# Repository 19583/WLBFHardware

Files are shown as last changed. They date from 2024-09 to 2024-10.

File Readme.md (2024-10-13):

<!--
 * @Date: 2024-09-03 09:58:07
 * @LastEditors: Towers
 * @LastEditTime: 2024-10-13 19:57:09
-->

# WLBF Hardware

合肥工业大学宣城校区摩托组宛陵毕方硬件部分开源  
更新应该告一段落了  

### 文件目录说明

```
WLBFHardware 
├── 01_DRV8701Driver        #双电机驱动
│  ├── 01_DRV8701Driver.pdf #工程原理图
│  ├── ASM                  #组装/贴片坐标
│  ├── BOM                  #物料表    
│  ├── CAM                  #Gerber文件
│  ├── PRJ                  #项目文件
├── 02_PowerPart            #电源部分
├── 03_SigPart              #信号部分
├── 04_InterfacePart        #编码器、摄像头一体转接板
├── 05_LightDriver          #灯板驱动
├── 06_B&RLight             #红蓝双色灯板
├── LICENSE                 #开源许可
├── Readme.md

```

### 作者

Towers  

qq:1946459294    

 *您也可以在贡献者名单中参看所有参与该项目的开发者。*

### 版权说明

该项目签署了GUN 授权许可，详情请参阅 [LICENSE.txt](https://github.com/19583/WLBFHardware/blob/main/LICENSE)

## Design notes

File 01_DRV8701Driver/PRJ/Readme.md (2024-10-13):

<!--
 * @Date: 2024-10-13 19:29:54
 * @LastEditors: Towers
 * @LastEditTime: 2024-10-13 19:35:22
-->
# DRV8701Driver  
该板是用AD22画的，有元件库依赖的问题，还不知道怎么解决，未来研究明白了可以考虑开源  
这只是个DRV8701双驱，也没有做电流采样，而且设计上我觉得有些小问题，相关的开源很多，大家可以多看看，打板完如果不能正常工作，第一个应该检查焊接，第二个可以重点关注nFault引脚电平以及DataSheet上的相关描述（TI的手册还是写的很好的）

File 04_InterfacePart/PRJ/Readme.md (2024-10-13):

<!--
 * @Date: 2024-10-13 19:13:34
 * @LastEditors: Towers
 * @LastEditTime: 2024-10-13 19:23:15
-->
# 04_InterfacePart  
该板同时集成了编码器转接板和摄像头转接板  
但是输入端MX1.25的线序是反的，后续是靠反焊接口解决的  
有想改回来，但是一方面时间安排紧张，另方面我们也因为各种原因放弃了速度闭环，就没有继续改，所以现在我这里也是个半拉工程  
因此这部分就不放工程文件和贴片坐标文件，只放改之前的原理图、打板文件和BOM表了

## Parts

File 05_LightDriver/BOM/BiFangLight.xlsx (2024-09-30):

Comment | Description | Designator | Footprint | LibRef | Quantity
4.7uF 25V X5R | 贴片瓷片电容; MLCC; 0603(1608); | C1 | 0805C | 4.7uF 0603 25V X5R | 1
100nF 50V X7R | 贴片瓷片电容; MLCC; 0603(1608); | C2, C5, C6 | 0805C | 100nF 0603 50V X7R | 3
470nF 50V X7R | 贴片瓷片电容; MLCC; 0603(1608); | C3, C4 | 0805C | 470nF 0603 50V X7R | 2
LED_Dot_Matrix 7x15 | 逐飞科技 7x15 LED点阵 | D1 | LED_DOT_MATRIX 7X15 | LED_Dot_Matrix 7x15 | 1
Header-D-M 2x11P | 2x11pin, 直插, 双排针 | P1 | HDR2X11-M | Header-D-M 2x11P | 1
AO3401 | P-Channel SOT-23 MOSFET | Q1, Q2, Q3, Q4, Q9, Q10, Q11 | SOT-23 | AO3401 | 7
S8050 | NPN 三极管 | Q5, Q6, Q7, Q8, Q12, Q13, Q14 | SOT-23 | NPN S8050 | 7
3.3K ±1% | 贴片电阻 | R1, R2 | 0805_Res | Res-Chip_1 | 2
4.7K ±1% | 贴片电阻 | R3 | 0805_Res | Res-Chip | 1
1K ±1% | 贴片电阻 | R4, R5, R7, R9, R11, R13, R15, R17 | 0805_Res | Res-Chip_3 | 8
10K ±1% | 贴片电阻 | R6, R8, R10, R12, R14, R16, R18, R24 | 0805_Res | Res-Chip_2 | 8
100R ±1% | 贴片电阻 | R19 | 0805_Res | Res-Chip_4 | 1
100K ±1% | 贴片电阻 | R20, R21, R22, R23 | 0805_Res | Res-Chip_5 | 4
TLD7002-16ES | TLD7002-16ES LED驱动芯片 | U1 | TSDSO-24 | TLD7002-16ES | 1
LMV321 | LMV321 单通道轨对轨运放 | U2 | SOT-23-5 | LMV321 | 1
ZX-PZ2.54-1-15PZZ | 插针结构:1x15P;间距:2.54mm;行距:-;圆针/方针:方针;安装类型:直插;排数:单排;总PIN位数:15P;额定电流:3A;额定电压:1kV;配合针长度:6mm;塑高:2.5mm;端接针长度:3mm;触头材质:黄铜;触头镀层:金;工作温度范围:-40℃~+105℃;焊接温度(最大值):-;颜色:黑色; | U3 | HDR-TH_15P-P2.54-V-M | ZX-PZ2.54-1-15PZZ | 1

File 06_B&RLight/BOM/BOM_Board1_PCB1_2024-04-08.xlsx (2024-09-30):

No. | Quantity | Designator | Comment | Footprint | Value
1 | 1 | H1 | PZ254-1-14-Z-8.5 | HDR-TH_14P-P2.54-V-M
2 | 105 | LED1,LED2,LED3,LED4,LED5,LED6,LED7,LED8,LED9,LED10,LED11,LED12,LED13,LED14,LED15,LED16,LED17,LED18,LED19,LED20,LED21,LED22,LED23,LED24,LED25,LED26,LED27,LED28,LED29,LED30,LED31,LED32,LED33,LED34,LED35,LED36,LED37,LED38,LED39,LED40,LED41,LED42,LED43,LED44,LED45,LED46,LED47,LED48,LED49,LED50,LED51,LED52,LED53,LED54,LED55,LED56,LED57,LED58,LED59,LED60,LED61,LED62,LED63,LED64,LED65,LED66,LED67,LED68,LED69,LED70,LED71,LED72,LED73,LED74,LED75,LED76,LED77,LED78,LED79,LED80,LED81,LED82,LED83,LED84,LED85,LED86,LED87,LED88,LED89,LED90,LED91,LED92,LED93,LED94,LED95,LED96,LED97,LED98,LED99,LED100,LED101,LED102,LED103,LED104,LED105 | XL-3528SURUGC | LED-SMD_4P-L3.2-W2.8-LS3.5-TL
3 | 1 | U1 | ZX-PZ2.54-1-15PZZ | HDR-TH_15P-P2.54-V-M

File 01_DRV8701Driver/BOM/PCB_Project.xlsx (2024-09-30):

Comment | Description | Designator | Footprint | LibRef | Quantity
HX SS12D10G4 |  | 1 | SW-TH_SHOU-HAN_SS12D10G4 | HX SS12D10G4 | 1 | 5
RVT220UF16V67RV0015 | 容值:220uF;精度:±20%;额定电压:16V;纹波电流:110mA@120Hz;等效串联电阻:-; | C1 | CAP-SMD_BD6.3-L6.6-W6.6-FD | RVT220UF16V67RV0015 | 1 | 5
1uF |  | C3, C4, C8, C12, C13, C15 | 0805C | C1608X7R1C105K | 6 | 30
100nF |  | C7, C9, C10, C11, C14, C16 | 0805C | C1608X7R1H104K | 6 | 30
1N5819WS S4_C2927280 |  | D1, D2 | SOD-323_L1.6-W1.3-LS2.7-RD | 1N5819WS S4_C2927280 | 2 | 10
红色 |  | DV1, DV2 | 0805D | LTST-C171GKT | 2 | 10
TPH1R403NL/CSD18532Q5B |  | Q1, Q2, Q3, Q4, Q5, Q6, Q7, Q8 | LQ_SON5X6 | CSD18532Q5B | 8 | 40
10K |  | R1, R4, R5, R6, R7, R8, R9, R10, R11 | 0805_RES | CRCW06034K99FKEA | 9 | 45
1K |  | R2, R3 | 0805_RES | CRCW06034K99FKEA, RES | 2 | 10
CON1 | Connector | SCROW1, SCROW2, SCROW3, SCROW4 | LQ_SCROW3&5MM | CON1 | 4 | 20
74HC125PW |  | U1 | LQ_TSSOP14-OPA4377AIPW | 74HC125PW | 1 | 5
DRV8701PRGER/DRV8701PRGER |  | U2, U3 | RGE0024F | DRV8701ERGER | 2 | 10
WAFER-GH1.25-6PWB | 插针结构:1x6P;间距:1.25mm;安装方式:卧贴;参考系列:GH;总PIN数:6P;排数:1;每排PIN数:6;额定电流:1A;工作温度范围:-25℃~+85℃; | U4 | CONN-SMD_6P-P1.25_XUNPU_WAFER-GH1.25-6PWB | WAFER-GH1.25-6PWB | 1 | 5
KF301-2P |  | 电源, 马达, 马达1 | LQ_PIN2 | 691 101 710 002 | 3 | 15

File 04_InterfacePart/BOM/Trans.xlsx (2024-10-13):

No. | Quantity | Designator | Comment | Footprint | Value
1 | 4 | C1,C2,C3,C4 | 2.2n | C0805 | 2.2n
2 | 2 | CN1,CN2 | PM254-2-03-S-8.5 | HDR-SMD_6P-P2.54-V-F-R2-C3-LS7.0
3 | 1 | H1 | FPC05018-09200 | FPC-SMD_FPC05018-09200
4 | 1 | H2 | PM254-2-08-S-8.5 | HDR-SMD_16P-P2.54-V-F-R2-C8-LS7.1
5 | 4 | Q1,Q2,Q3,Q4 | S8050 | SOT-23-3_L2.9-W1.6-P1.90-LS2.8-BR
6 | 4 | R1,R5,R8,R12 | 100R | R0805 | 100R
7 | 8 | R2,R3,R6,R7,R9,R10,R13,R14 | 4.7k | R0805 | 4.7k
8 | 2 | R4,R11 | 330R | R0805 | 330R
9 | 2 | U1,U2 | MX1.25-4PWB | CONN-SMD_4P-P1.25_WAFER-MX1.25-4PWB

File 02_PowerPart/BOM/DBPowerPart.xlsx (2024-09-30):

No. | Quantity | Designator | Comment | Footprint | Value
1 | 4 | C6,C7,C8,C9 | 10uF | C0805 | 10uF
2 | 2 | C12,C18 | 220uF | CAP-SMD_BD6.3-L6.6-W6.6-FD | 220uF
3 | 6 | C13,C20,C21,C22,C23,C24 | 4.7uF | C0805 | 4.7uF
4 | 4 | C14,C15,C19,C25 | 100nF | C0805 | 100nF
5 | 1 | C16 | 47uF | C1206 | 47uF
6 | 4 | C27,C28,C29,C30 | 47uF | C0805 | 47uF
7 | 2 | C31,C32 | 4.7nF | C0805 | 4.7nF
8 | 1 | CN1 | XT30PW-M | CONN-TH_XT30PW-M
9 | 2 | H3,H4 | PM254-2-08-S-8.5 | HDR-SMD_16P-P2.54-V-F-R2-C8-LS7.1
10 | 2 | Q3,Q4 | AMS1117-3.3V | SOT-89-3_L4.5-W2.5-P1.50-LS4.2-BR
11 | 2 | R36,R45 | 200k | R0805 | 200k
12 | 2 | R37,R41 | 20k | R0805 | 20k
13 | 1 | R38 | 15k | R0805 | 15k
14 | 1 | R39 | 10kΩ | RES-ADJ-TH_3P-L10.0-W10.0-P2.50-L | 10kΩ
15 | 1 | R40 | 3.3k | R0805 | 3.3k
16 | 1 | R43 | 53.6k | R0603 | 53.6k
17 | 1 | R44 | 10.2k | R0603 | 10.2k
19 | 2 | U25,U29 | 4.7uH | IND-SMD_L7.2-W6.6_GPSR07X0 | 4.7uH
20 | 2 | U26,U28 | SCT2450STER | ESOP-8_L4.9-W3.9-P1.27-LS6.0-BL-EP
21 | 2 | U30,U31 | XT30PW-F20.G.Y | CONN-TH_XT30PW-F-1
22 | 1 | U33 | HX SS12D10G5-WJ | SW-TH_3P-P4.80_HX-SS12D10G5-WJ

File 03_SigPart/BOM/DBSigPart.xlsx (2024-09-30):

No. | Quantity | Designator | Comment | Footprint | Value
1 | 4 | 3V3电源指示,5V电源指示,VBAT电源指示,摄像头电源指示 | NCD0805R1 | LED0805-RD
2 | 1 | BUZZER1 | SFN-1270-0540-35P5.0 | BUZ-TH_BD12.5-P5.00-D0.9
3 | 1 | C19 | 100nF | C0805 | 100nF
4 | 1 | H4 | PM2.54-1*4 | HDR-TH_4P-P2.54-V-F
5 | 2 | H5,H6 | H5,H6 | HDR-SMD_6P-P2.54-V-M-R2-C5-S7.4 |  | √
6 | 1 | H8 | PM254V-11-03-H85 | HDR-TH_3P-P2.54-V-F
7 | 1 | H9 | PM254-2-08-S-8.5 | HDR-SMD_16P-P2.54-V-F-R2-C8-LS7.1 |  | √
8 | 1 | P1 | 2.54-1*8P母环保 | HDR-TH_8P-P2.54-V-F-1 |  | √
9 | 2 | P2,P3 | 2.54-2*8P针 | HDR-TH_16P-P2.54-V-M-R2-C8-S2.54 |  | √
10 | 1 | Q1 | S9013 J3 | SOT-23-3_L2.9-W1.3-P1.90-LS2.4-BR |  | √
11 | 14 | R4,R6,R7,R8,R9,R10,R11,R12,R13,R14,R15,R16,R45,R46 | 4.7k | R0805 | 4.7k
12 | 1 | R20 | 10R | R0805 | 10R | √
13 | 2 | R21,R44 | 10k | R0805 | 10k
14 | 1 | R41 | 100 | R0805 | 100
15 | 1 | R43 | 30k | R0805 | 30k
16 | 4 | SW1,SW2,SW3,SW4 | SW1,SW2,SW3,SW4 | SW-SMD_4P-L4.2-W3.3-P2.15-LS5.1 |  | √
17 | 1 | TOF1 | XH-6直插 | CONN-TH_6P-P2.50_XH-6A |  | √
18 | 1 | U1 | TC264核心板COPY | TC264逐飞
19 | 1 | U30 | GT-TCA06F-H050-L1 | KEY-SMD_GT-TCA06F-H050-L1
20 | 1 | U31 | PM2.54-2*4 | HDR-TH_8P-P2.54-V-F-R2-C4-S2.54
21 | 1 | U35 | DW254W-22-22-85 | CONN-TH_22P-P2.54_DEALON_DW254W-22-22-85 |  | √
22 | 1 | U36 | ZX-XH2.54-8PWZ | CONN-TH_8P-P2.50_ZX-XH2.54-8PWZ
23 | 1 | 电机驱动1 | WAFER-GH1.25-6PWB | CONN-SMD_6P-P1.25_XUNPU_WAFER-GH1.25-6PWB

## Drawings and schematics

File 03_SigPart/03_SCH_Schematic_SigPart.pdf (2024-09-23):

# 3V_OTHERS ENCODER¹A

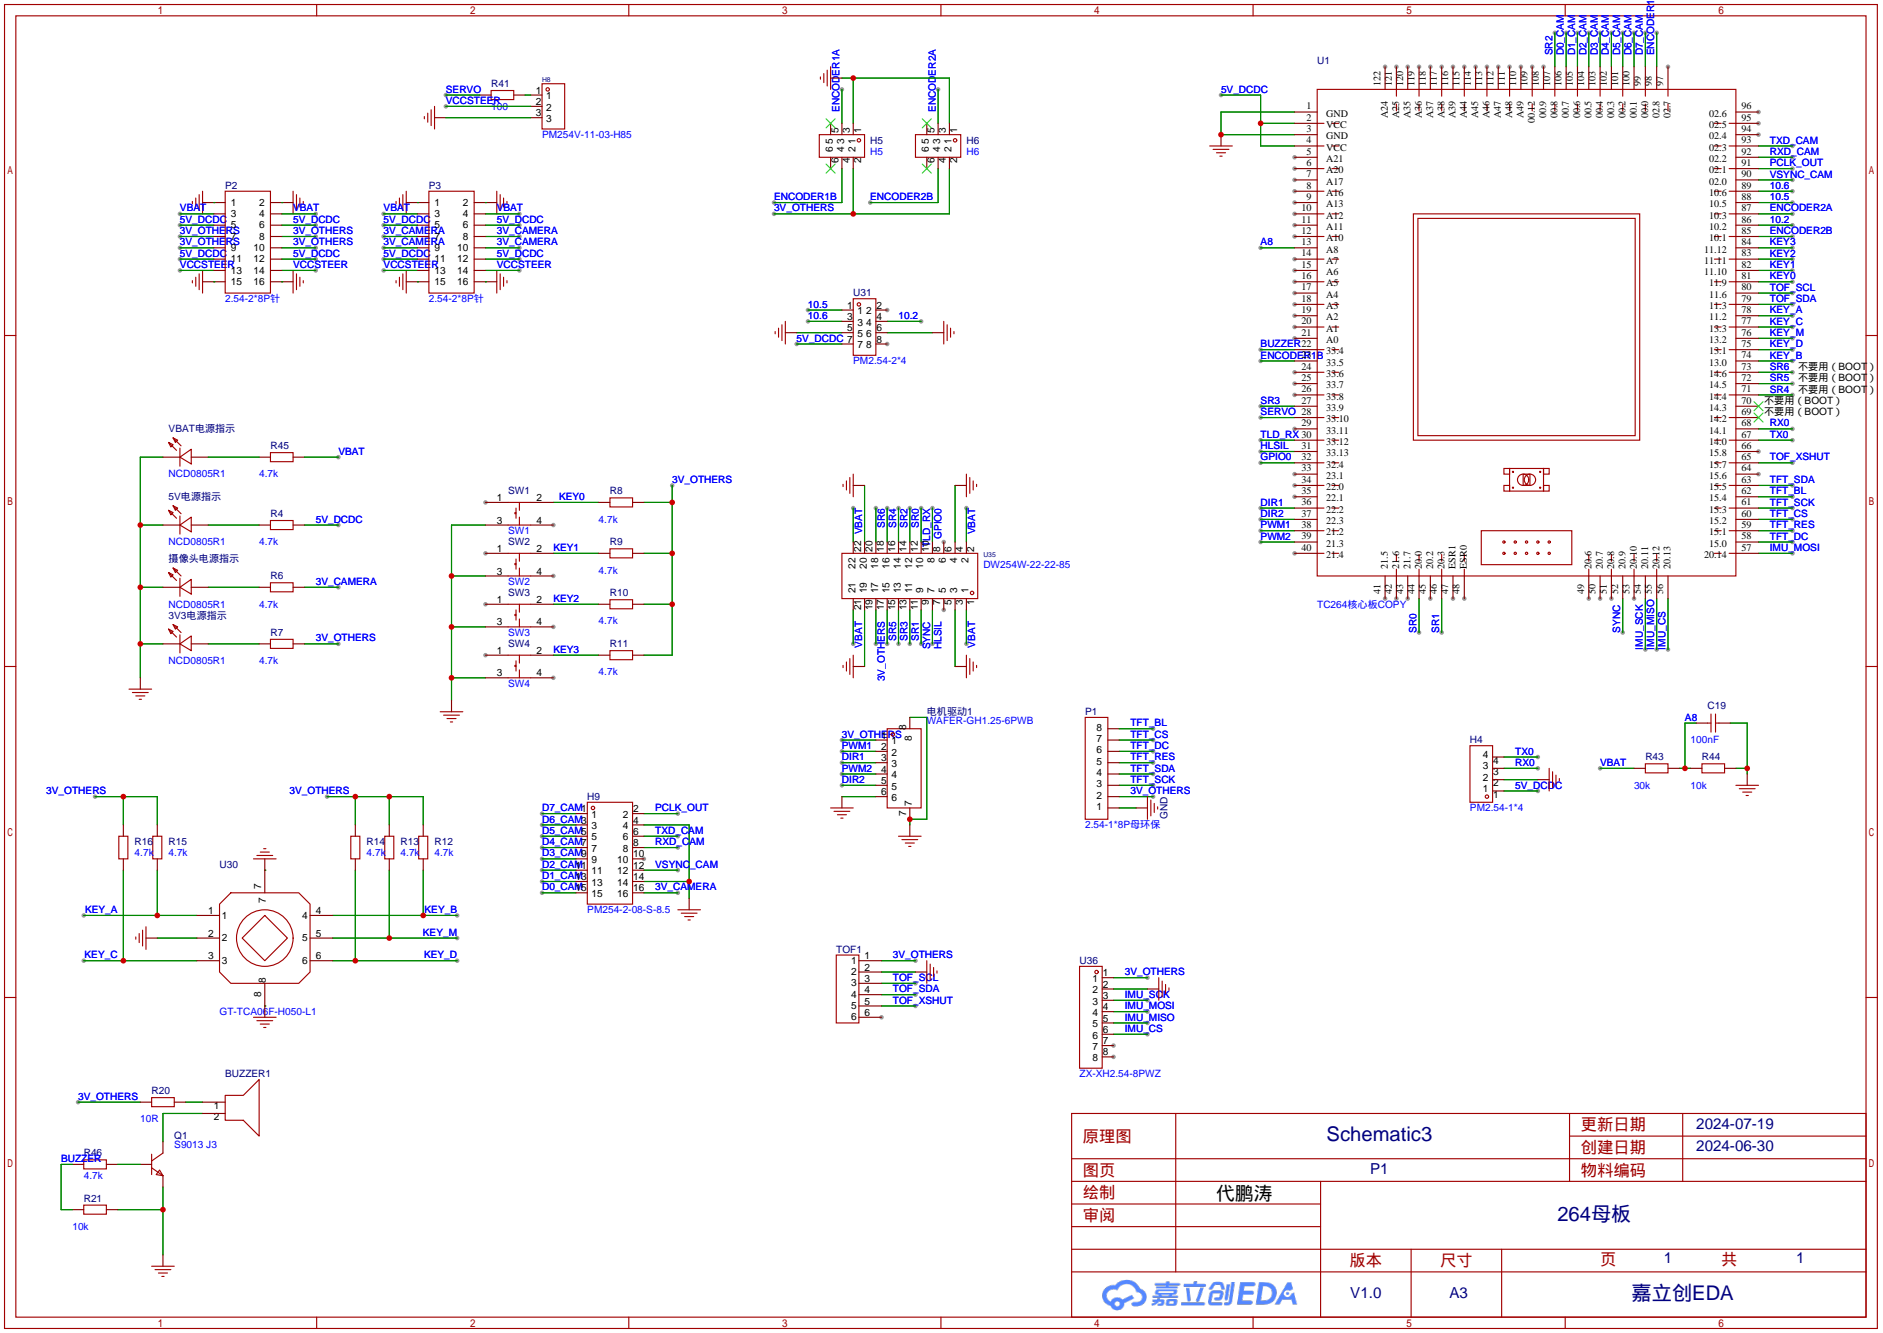
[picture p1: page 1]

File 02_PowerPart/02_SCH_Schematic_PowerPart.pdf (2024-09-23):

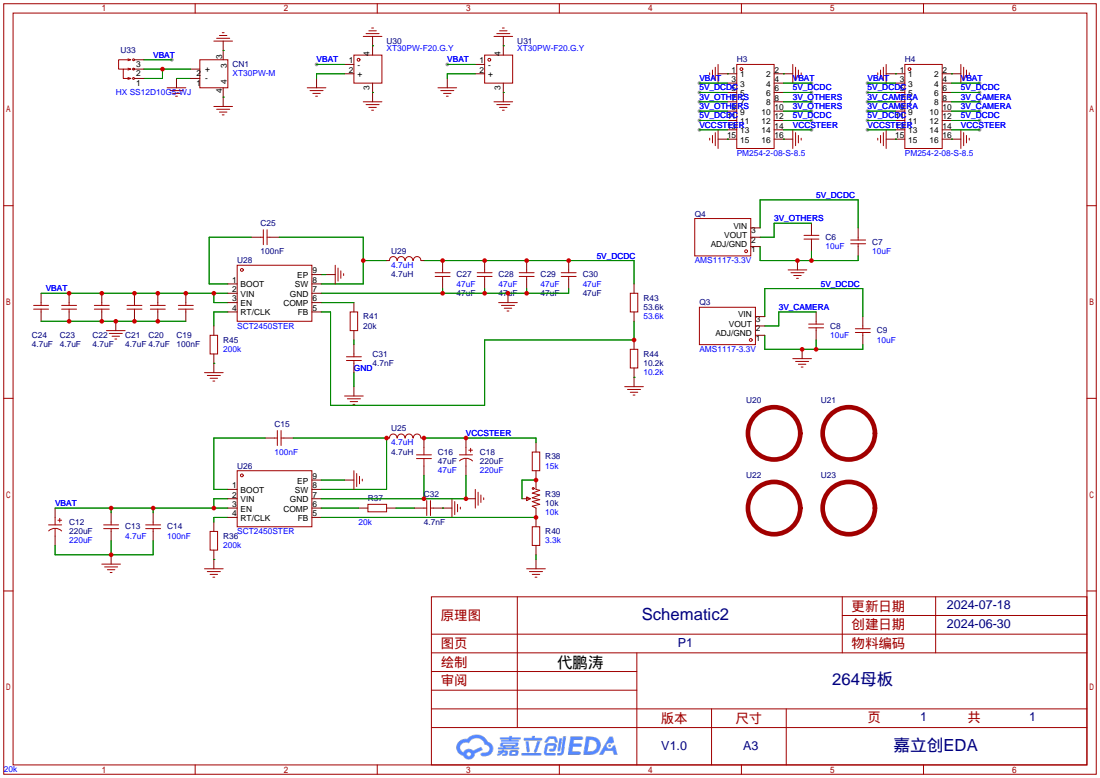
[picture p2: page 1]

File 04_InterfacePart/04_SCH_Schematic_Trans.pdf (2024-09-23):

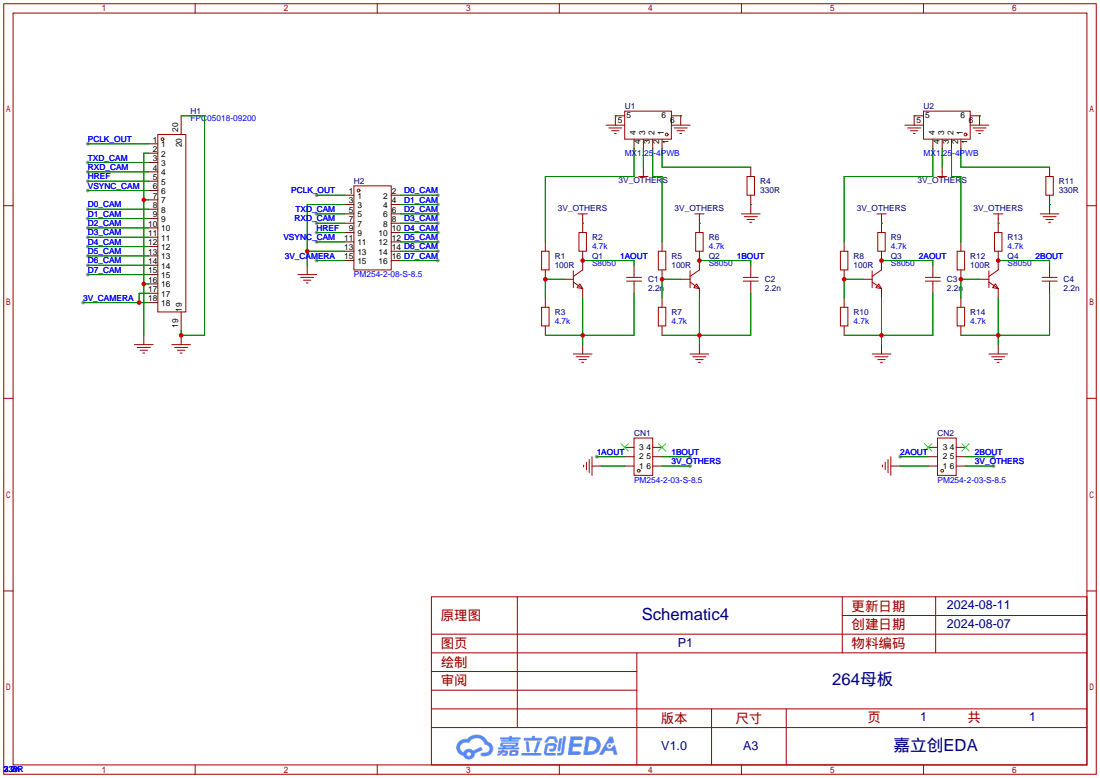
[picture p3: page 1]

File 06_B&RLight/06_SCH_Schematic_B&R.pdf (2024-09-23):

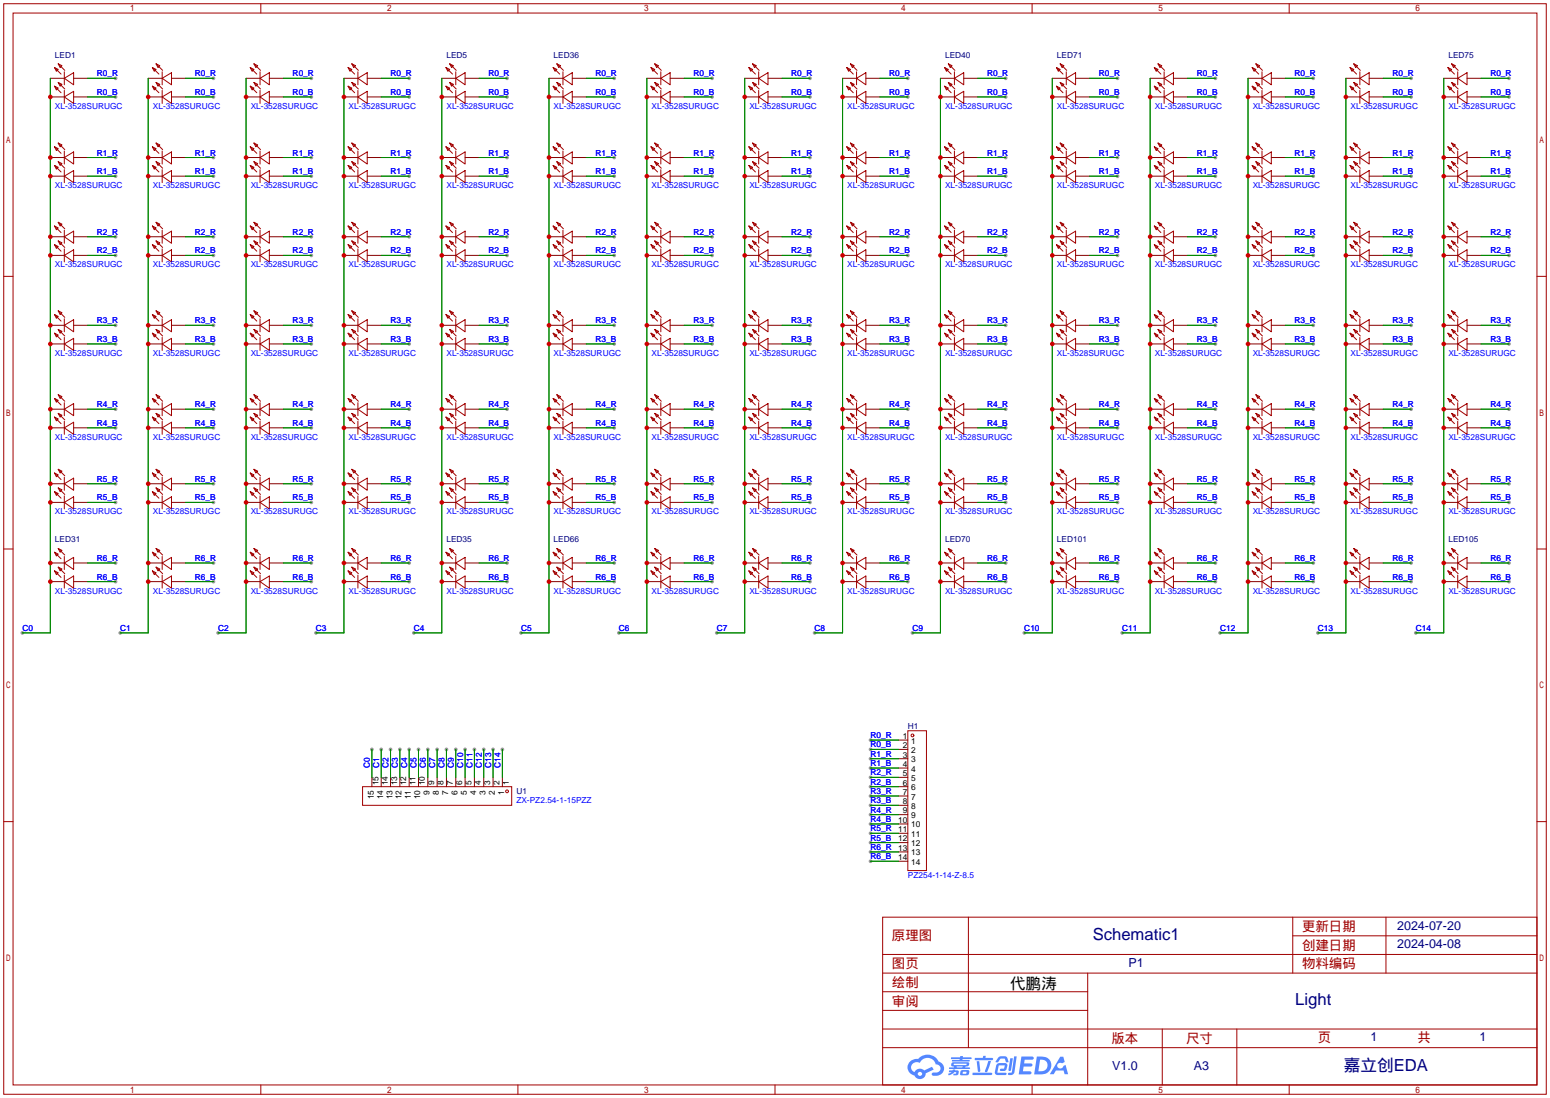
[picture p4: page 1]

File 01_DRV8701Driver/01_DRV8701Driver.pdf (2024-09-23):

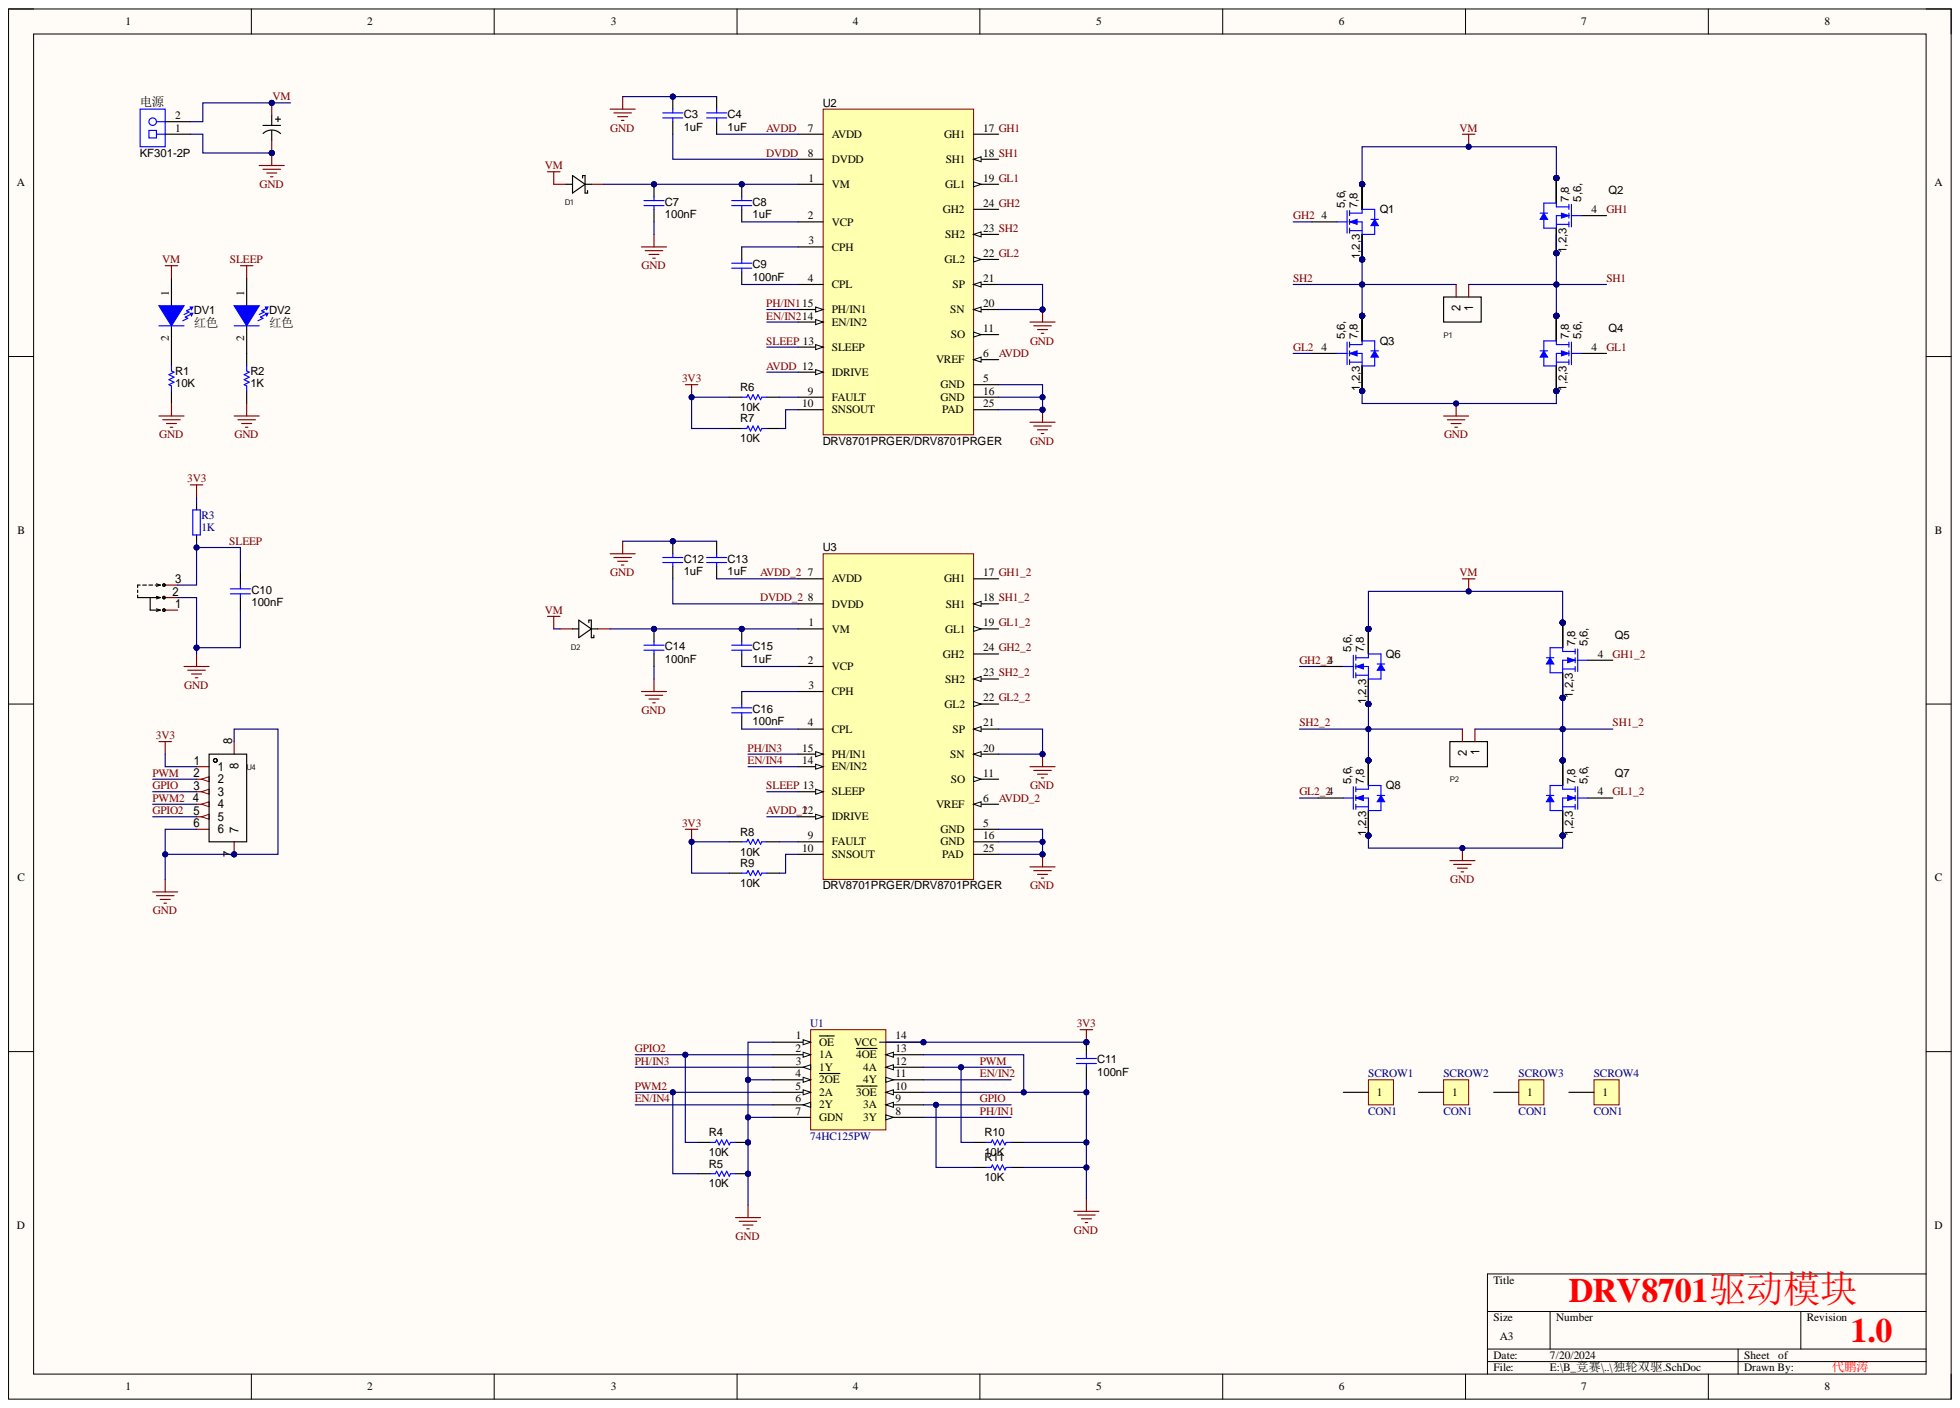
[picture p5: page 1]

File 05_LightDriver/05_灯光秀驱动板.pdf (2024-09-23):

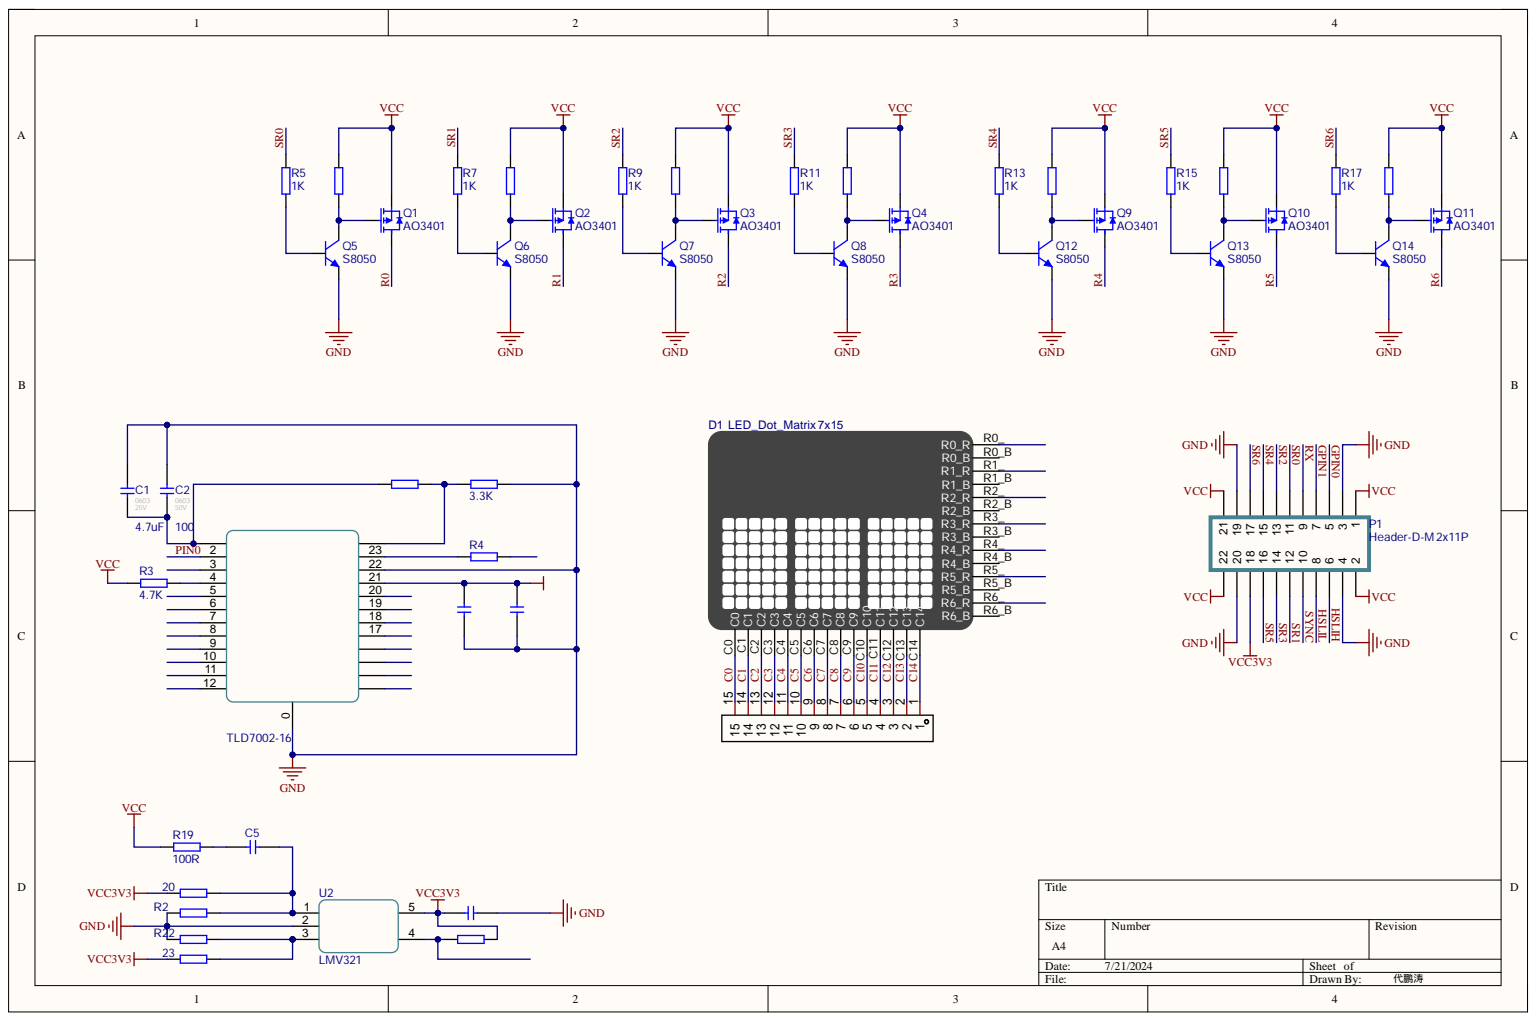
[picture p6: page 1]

X7R 10K | SYNC

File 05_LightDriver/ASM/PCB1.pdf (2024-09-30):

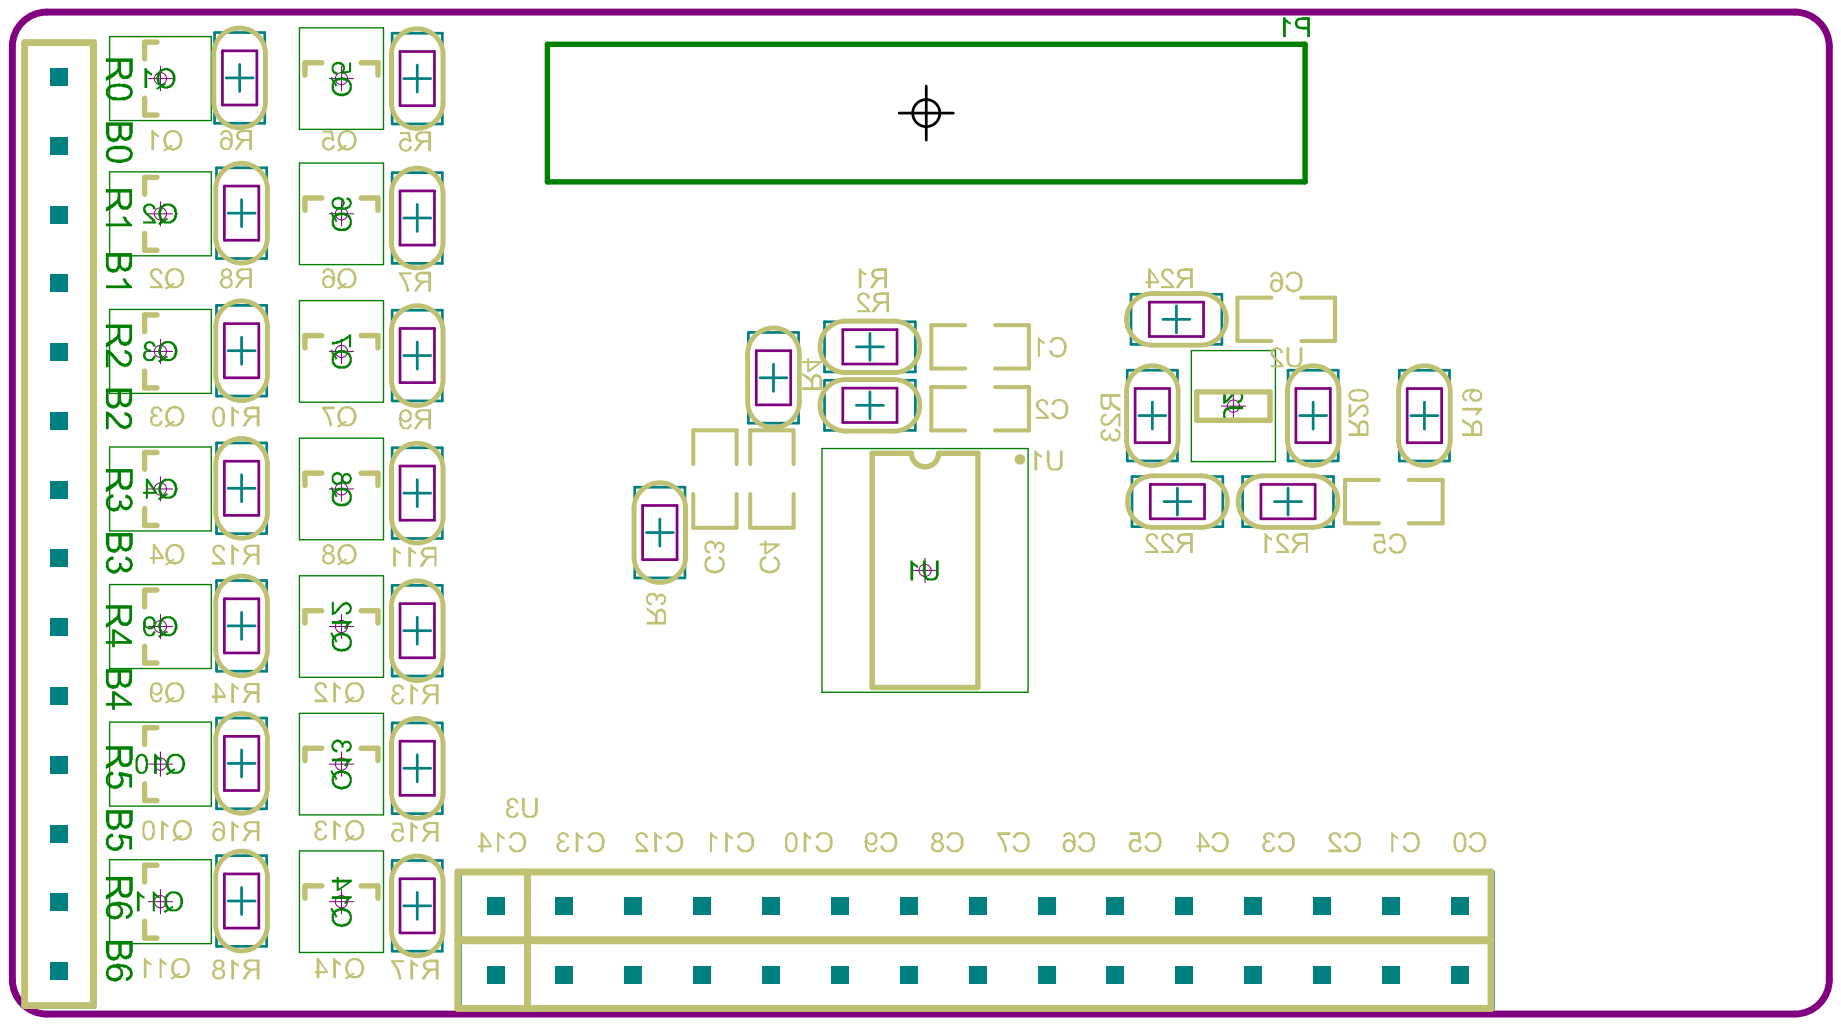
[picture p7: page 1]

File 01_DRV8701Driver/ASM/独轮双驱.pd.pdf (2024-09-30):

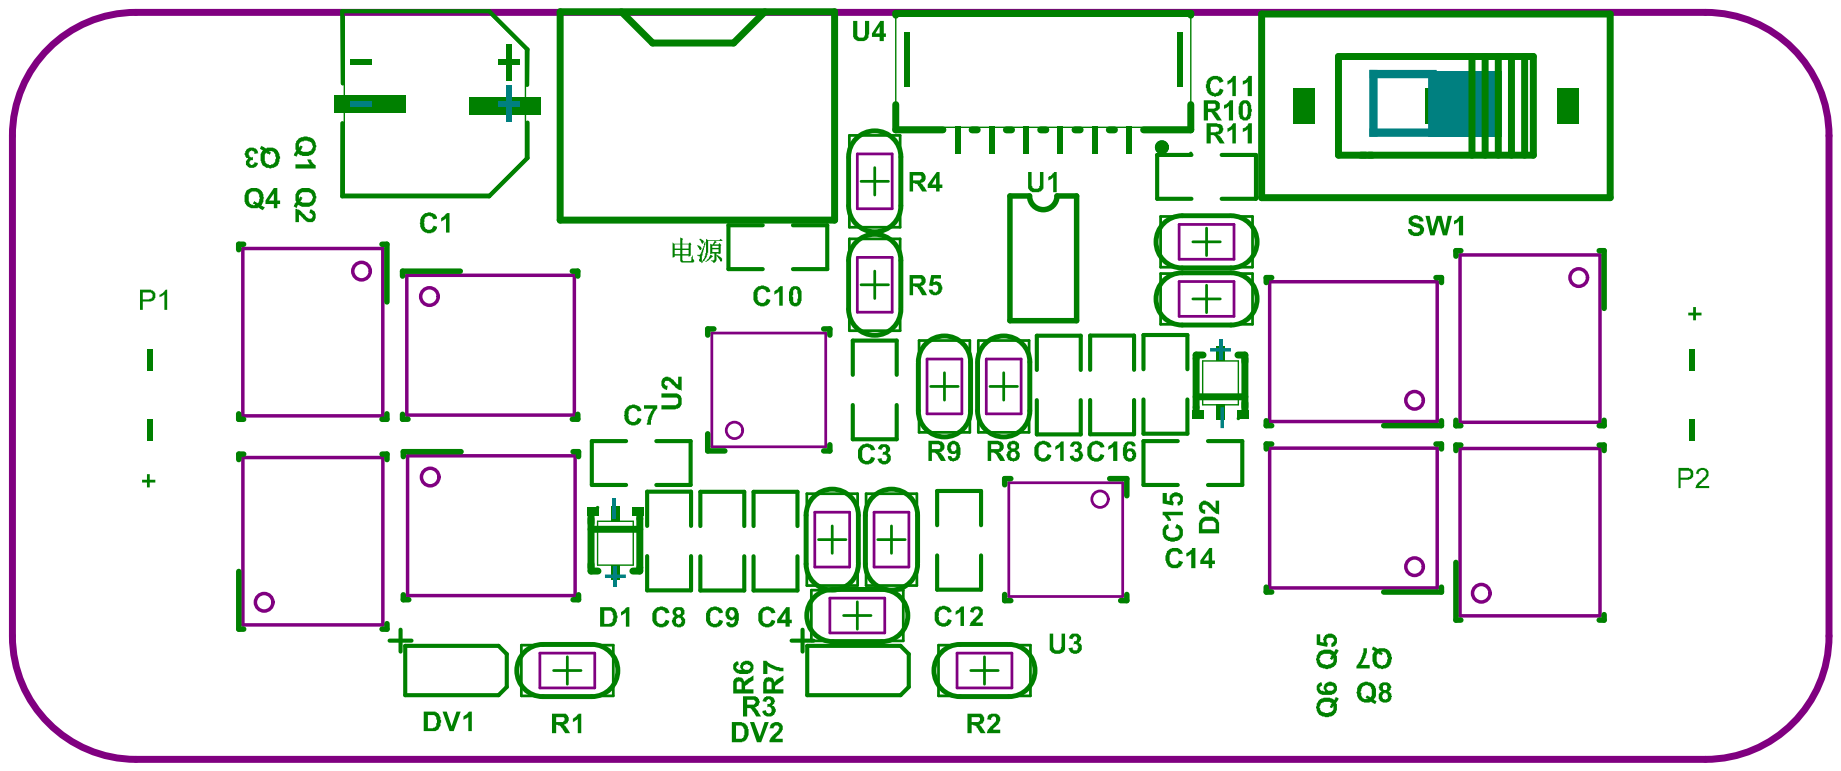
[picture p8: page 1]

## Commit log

2024-09-23 添加LISENSE和Readme
2024-09-23 “添加许可证链接”
2024-09-30 补充了Gerber文件和贴片坐标文件
    [PCB_Project.xlsx, Pick Place for 独轮双驱.csv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]
2024-09-30 补充了Gerber文件和SMT坐标文件
    [BOM_Board1_PCB1_2024-04-08.xlsx, BiFangLight.xlsx, DBPowerPart.xlsx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]
2024-10-13 Last commit 补充了工程文件
    [Pick Place for PCB1.csv, Trans.xlsx]
